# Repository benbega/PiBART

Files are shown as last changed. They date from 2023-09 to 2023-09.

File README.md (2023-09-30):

## Introduction
As a lifelong resident of the Bay Area, I have seen countless BART trains fly by, always giving off their signature high pitched howl as they barrel down the tracks. BART is a very unique urban transportation system, and although it is not the most efficient, I have grown to love riding it between the East Bay and San Francisco. 

The project outlined below is a fully custom model train, based off of the BART system. It was built to showcase skills in multiple facets of electrical engineering, as well as to be a homage to the legendary train.

A brief example of the train running can be seen [here](https://youtu.be/NTuRKBK8t7I)

## System Breakdown
At a high level, this project can be broken down into the following four major subsystems:

 1. Train Electronics
 2. Train Chassis
 3. Track Electronics
 4. Track Design

At the current time of writing, I am working on version 2 of the project, so the subsystem descriptions below will correspond to that version.

### Train Electronics
The train houses the entirety of the electronics it needs to operate autonomously. The main processing is all done on a Raspberry Pi 4B+, that is powered by a Geekworm X728 uninterruptable power supply (UPS) with two 18650 batteries. In order to know where it is located on the tracks, the Raspberry Pi is connected to an RC522 RFID sensor via SPI. The RFID tags are embedded in the tracks, and are manually preset to have "full speed", "slow", or "medium speed" values. After detecting these tags, the RFID sensor communicated back to the Raspberry Pi and the train enters the speed level corresponding to the tag.

In order to control the motor, the Raspberry Pi outputs logic signals to a custom PCB based around the L293D IC. The PCB has six logic inputs, external power input, two motor output terminals, and two status LEDs for debugging. The PCB is fully custom designed in KiCAD and was fabricated by PCBWay. The PCB can officially support up to 1A for each motor channel, but this number could possibly be higher in the future after some testing and possible integrating a cooling solution.

The train operates using a live third rail, which is currently running at 12V DC. Power from the third rail feeds in from two wires mounted on a side bracket (details on the mount can be found in the following section) and into the power delivery PCB and the Raspberry Pi UPS. The power is stepped down from the 12V to 5V with a simple DC-DC converter to match the needed input on the UPS. In the built configuration, the third rail is continually charging the battery cells on the UPS, which in turn power the Raspberry Pi. Since there are no metal tracks to ground the system, there is a hidden "fourth rail" running in the middle of the trackbed. An identical connection is made from the train to this rail in order to ground the system. 

The drivetrain of the train is based around a single DC motor that can be run in the 5-12V range. More about the drivetrain can be found in the *Train Chassis* section below.

### Train Chassis
The train chassis is entirely custom designed, using a mix of OnShape and TinkerCAD depending on the complexity of the parts. All elements of the chassis are 3d printed except for the ball bearings, which were purchased preassembled. The main chassis of the train is a flat plane with cutouts for the gears (more on those later). The top of the chassis features a slide mount for the Raspberry Pi and a vertical mounting bracket for the power delivery PCB, as well as a mount for the DC motor. In order to transfer power from the live third rail, there is a side mounted bracket to guide wires down from the Raspberry Pi and power delivery PCB. An identical mount runs through the gear cutout on the chassis to provide the ground line connections. The bottom of the chassis is reinforced with 3 extra strips of PLA running along the length of the train, while also featuring mounts for the bearings. The two axles are 1/4" diameter and have wheels friction fit on either end. The train wheels are conical in shape, with an exaggerated flange for extra stability on the small scale.

The drivetrain of the system consists of a DC motor with a 10 tooth gear and a 15 tooth gear mounted on the rear axle. A pulley is used to transfer power between the gears. The current gear ratio is still being iterated on, to find the right performance level for the scale.

### Track Electronics
The trackbed electronics are very simple in theory, but are currently difficult to maintain. The live third rail and grounding fourth rail are both 3d printed from PLA, with a layer of conductive copper tape stuck to the top of each. This copper tape preforms good enough for my needs, with about 5 ohms of resistance measured over 20 inches of rail. The downside of using the copper tape to add conductivity to the rails is its general structural weakness. The tape tears very easily, and wears out over time with the wires from the train car rubbing against it. Adding more tape on top of the worn tape can fix these problems, but also sometimes results in a loss of conductivity along the rail.

In order for the train to control itself, RFID tags are laid within the trackbed, between sleeper planks. Standard 13.56MHz RFID tags are used, in order to keep the system lower cost and less complex.

Power is provided to the third rail and grounding rail at one end of the trackbed, with a standard bench power supply.

### Track Design
The trackbed is a simple 3 rail design, with a small fourth rail running down the center of the tracks. The main rails are spaced with 3.375" between the center of each rail, with the third rail being 1.125" to the right of the trackbed. Each rail segment is 5" in length, and is supported by a sleeper plank at each end. The overall track dimensions were built out after the train chassis was assembled, to ease the design constraints on that part of the project.

## Current Features
The train currently can operate autonomously on a straight section of track, with the third rail running at 12V. A command is issued to the train to start moving initially, and then the Raspberry Pi takes over and controls the train's speed by reading RFID tags, as mentioned above. The train can slow down, speed up, and come to a complete stop autonomously. 

## Future Work
As of September 2023, I am working on optimizing the drivetrain of the system so it runs smoother along the rails. I am currently experimenting with ways of adding grip to the tracks, as well as with ways to better contact the third rail for more consistent power delivery. After these two parts of the system are finished, I will begin experimenting with the train's turn radius to find a suitable dimension to build curved sections of track. I anticipate this will be a longer process, and plan on building out a longer section of straight track simultaneously, to optimize the train control system and find the speed limits of the system. 

### End Notes
I will also be updating this GitHub repo with 3d models, code, images, and more over the coming weeks, so check back periodically if you are interested in the project. 

**I am also looking for work in the electrical engineering field, feel free to reach out if you have any leads.**

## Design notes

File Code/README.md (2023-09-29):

## Code Information

### GPIOZero
All code for this project is written in Python3, on a Raspberry Pi 4B+ running Raspbian. The [GPIOZero](https://gpiozero.readthedocs.io/en/stable/installing.html) library is used to simplify the scripting.

Instructions for installing and setting up GPIO Zero can be found [HERE](https://gpiozero.readthedocs.io/en/stable/installing.html).

### MFRC522
The [mfrc522](https://github.com/pimylifeup/MFRC522-python) library is used to connect with the RFID sensor, and can be downloaded with the following command in Raspbian:

    sudo pip3 install mfrc522

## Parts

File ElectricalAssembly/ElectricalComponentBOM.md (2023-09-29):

## Electrical Component BOM

This BOM does not include the parts to assemble the power delivery PCB. Please refer to the PCB schematics for that component list.

### Components:
1. Raspberry Pi 4B+ (4GB Model)
2. Geekworm Raspberry Pi X728 18650 UPS & Power Management Board
3. 2x Panasonic NCR18650GA 3450mAh 10A Battery
4. Generic 6-12V DC Motor
5. RC522 RFID Sensor
6. Generic 13.56MHz RFID tags
7. DC barrel jack adapter with screw terminals

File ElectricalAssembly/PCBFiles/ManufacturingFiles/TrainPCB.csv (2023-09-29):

Source: | D:\KiCadProjects\RaspiCar_PCB2\RaspiCar_PCB1.kicad_sch
Date: | 10/15/2022 9:34:41 PM
Tool: | Eeschema (6.0.4)
Generator: | C:\Program Files\KiCad\6.0\bin\scripting\plugins/bom_csv_grouped_by_value_with_fp.py
Component Count: | 17
Ref | Qnty | Value | Cmp name | Footprint | Description | Vendor
C1, C2, | 2 | 1uF | C | Capacitor_SMD:C_Elec_5x5.4 | Unpolarized capacitor
H1, H2, H3, H4, | 4 | MountingHole | MountingHole | MountingHole:MountingHole_2.2mm_M2 | Mounting Hole without connection
L293D1, | 1 | L293D | L293D | Package_DIP:DIP-16_W7.62mm | Quadruple Half-H Drivers
LED1, | 1 | LED1 | LED | LED_THT:LED_D5.0mm | Light emitting diode
LED2, | 1 | LED2 | LED | LED_THT:LED_D5.0mm | Light emitting diode
Motor_1, | 1 | MotorTerminal1 | Screw_Terminal_01x02 | TerminalBlock:TerminalBlock_Altech_AK300-2_P5.00mm | Generic screw terminal, single row, 01x02, script generated (kicad-library-utils/schlib/autogen/connector/)
Motor_2, | 1 | MotorTerminal2 | Screw_Terminal_01x02 | TerminalBlock:TerminalBlock_Altech_AK300-2_P5.00mm | Generic screw terminal, single row, 01x02, script generated (kicad-library-utils/schlib/autogen/connector/)
PWR_GND1, | 1 | PWR_GND | Conn_01x02_Male | Connector_PinHeader_2.54mm:PinHeader_1x02_P2.54mm_Vertical | Generic connector, single row, 01x02, script generated (kicad-library-utils/schlib/autogen/connector/)
R1, R2, | 2 | 3.3k | R | Resistor_THT:R_Axial_DIN0207_L6.3mm_D2.5mm_P7.62mm_Horizontal | Resistor
Raspi_Logic1, | 1 | PiLogicHeaders | Conn_01x06_Male | Connector_PinHeader_2.54mm:PinHeader_1x06_P2.54mm_Vertical | Generic connector, single row, 01x06, script generated (kicad-library-utils/schlib/autogen/connector/)
Raspi_PWR1, | 1 | RaspiPWR/GND | Conn_01x02_Male | Connector_PinHeader_2.54mm:PinHeader_1x02_P2.54mm_Vertical | Generic connector, single row, 01x02, script generated (kicad-library-utils/schlib/autogen/connector/)
ServoPWR1, | 1 | ServoPWR/GND | Conn_01x02_Male | Connector_PinHeader_2.54mm:PinHeader_1x02_P2.54mm_Vertical | Generic connector, single row, 01x02, script generated (kicad-library-utils/schlib/autogen/connector/)

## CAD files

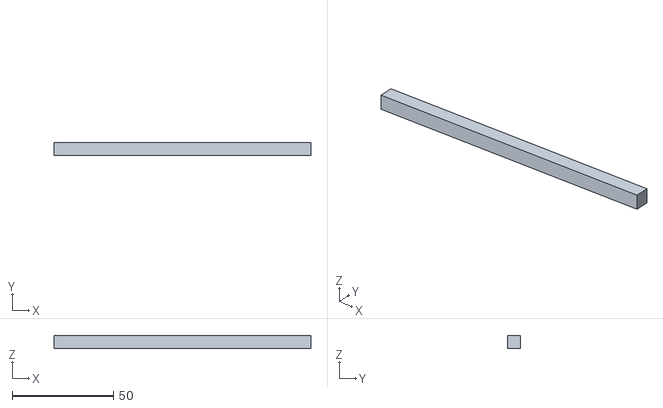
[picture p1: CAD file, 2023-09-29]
PhysicalAssembly/TrackAssemblyComponents/MainRail.stl
127.0 x 6.35 x 6.35

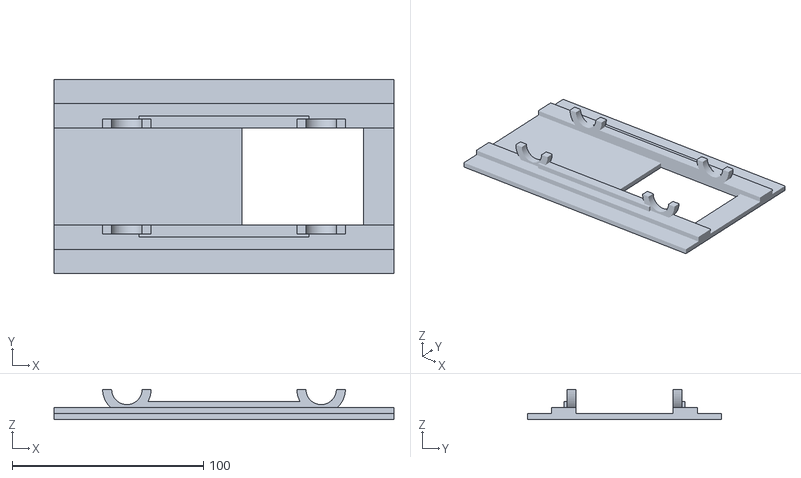
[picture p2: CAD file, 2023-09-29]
PhysicalAssembly/TrainAssemblyComponents/MainChassis.stl
177.8 x 101.6 x 15.9

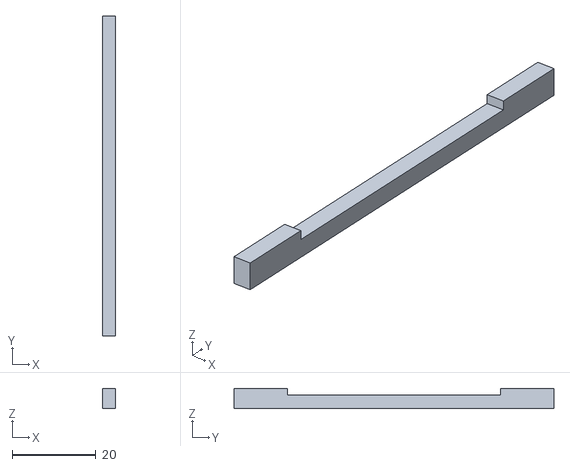
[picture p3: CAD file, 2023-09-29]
PhysicalAssembly/TrainAssemblyComponents/RFIDSensorMount.stl
3.18 x 76.2 x 4.76

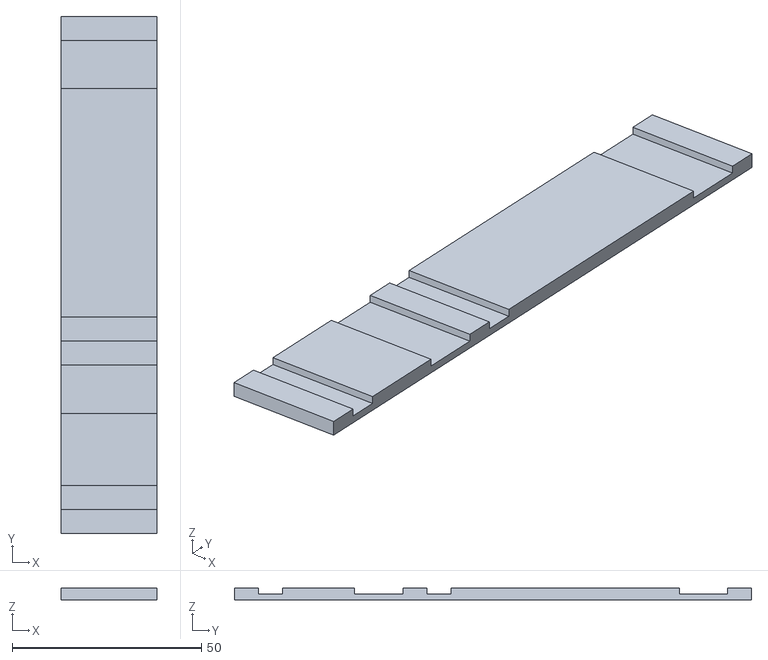
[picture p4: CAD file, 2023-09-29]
PhysicalAssembly/TrackAssemblyComponents/SleeperPlank.stl
25.4 x 136.5 x 3.17

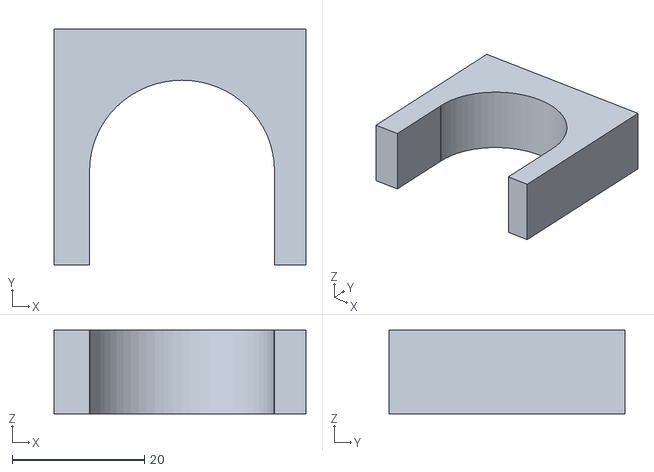
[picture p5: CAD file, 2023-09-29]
PhysicalAssembly/TrainAssemblyComponents/MotorMount.stl
38.1 x 35.7 x 12.7

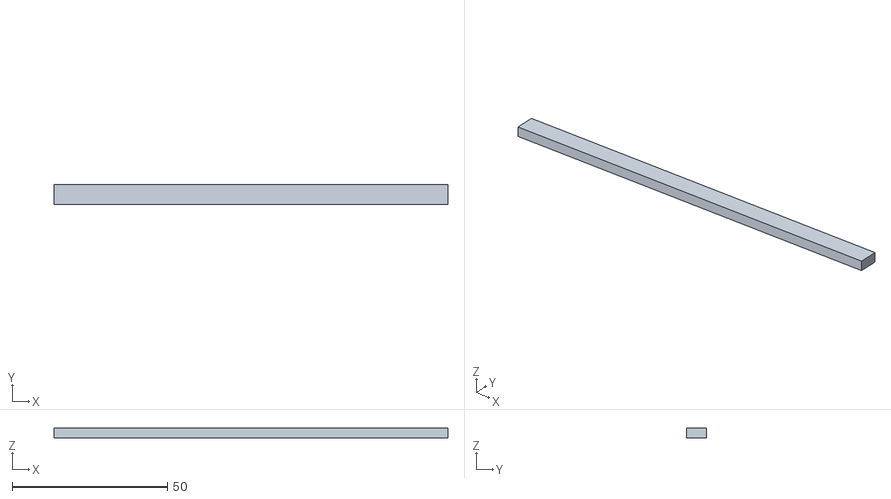
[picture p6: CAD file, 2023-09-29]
PhysicalAssembly/TrackAssemblyComponents/GroundingRail.stl
127.0 x 6.35 x 3.17

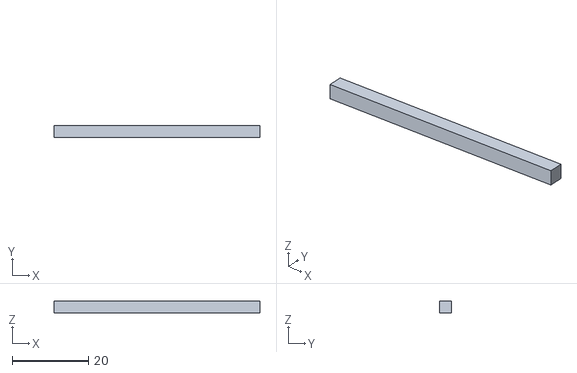
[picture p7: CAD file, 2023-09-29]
PhysicalAssembly/TrainAssemblyComponents/RaspberryPiMount.stl
54.0 x 3.18 x 3.17

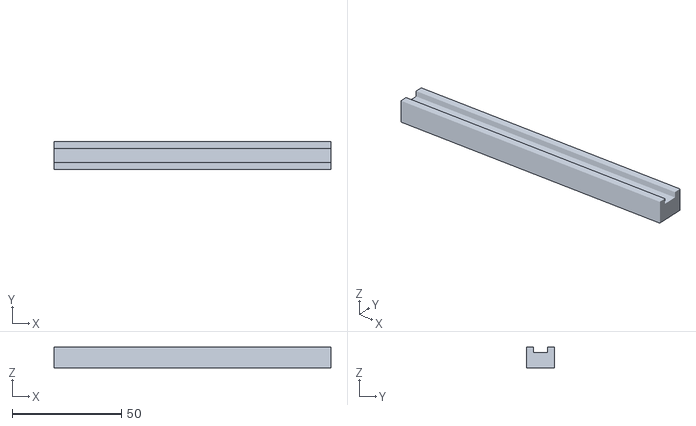
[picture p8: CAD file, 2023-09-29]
PhysicalAssembly/TrackAssemblyComponents/RailMount.stl
127.0 x 12.7 x 9.52

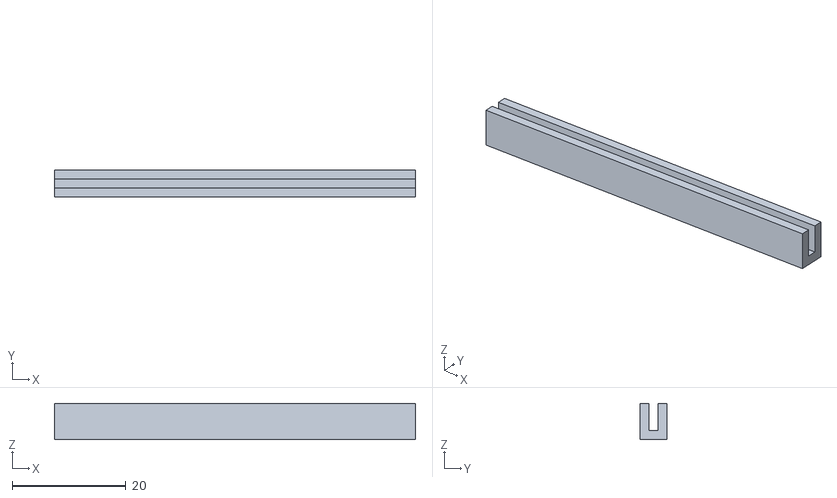
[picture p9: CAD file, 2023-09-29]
PhysicalAssembly/TrainAssemblyComponents/PowerDeliveryBoardMount.stl
63.5 x 4.76 x 6.35

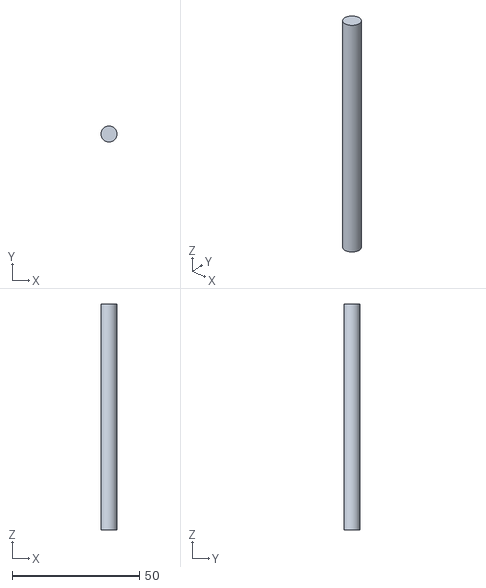
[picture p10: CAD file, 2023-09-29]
PhysicalAssembly/TrainAssemblyComponents/Axle.stl
6.35 x 6.35 x 88.9

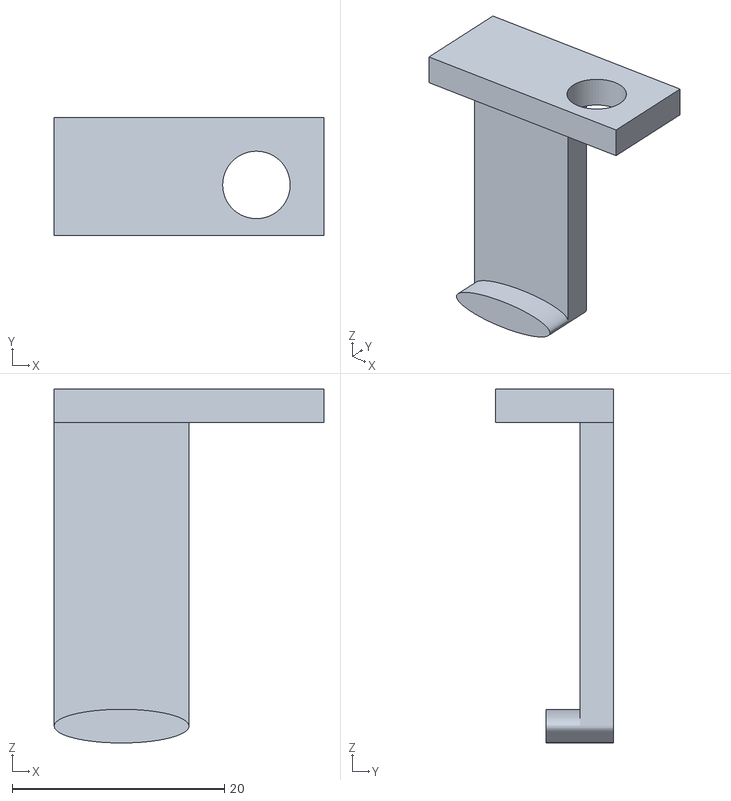
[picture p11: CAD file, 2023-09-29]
PhysicalAssembly/TrainAssemblyComponents/GroundingRailBoot.stl
25.4 x 11.1 x 33.3

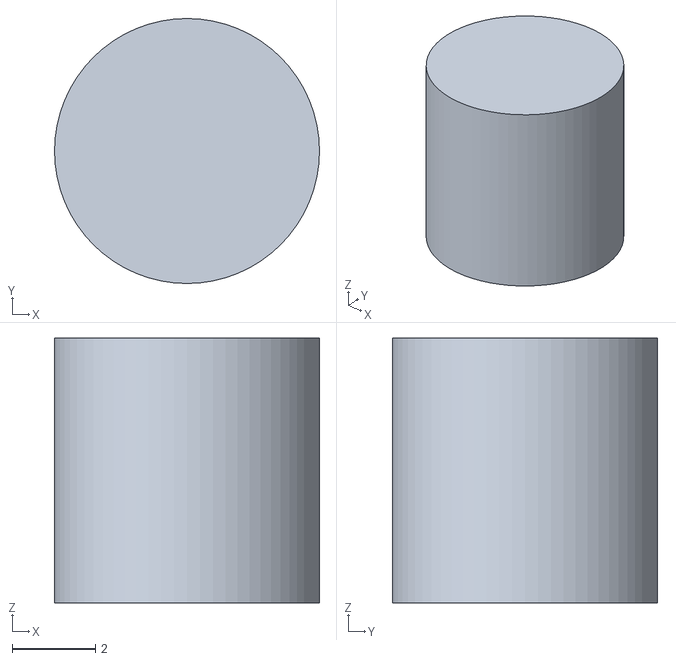
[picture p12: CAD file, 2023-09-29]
PhysicalAssembly/TrainAssemblyComponents/RailBootPivotMount.stl
6.35 x 6.35 x 6.35

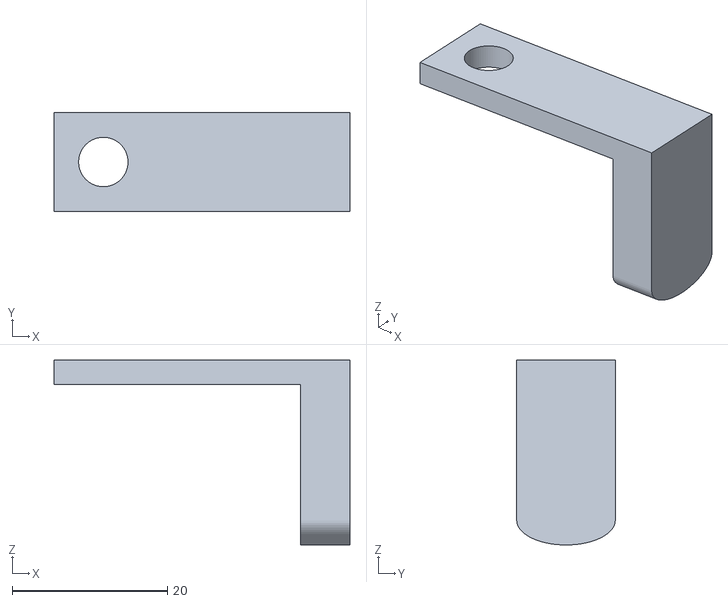
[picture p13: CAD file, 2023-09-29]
PhysicalAssembly/TrainAssemblyComponents/ThirdRailBoot.stl
38.1 x 12.7 x 23.8

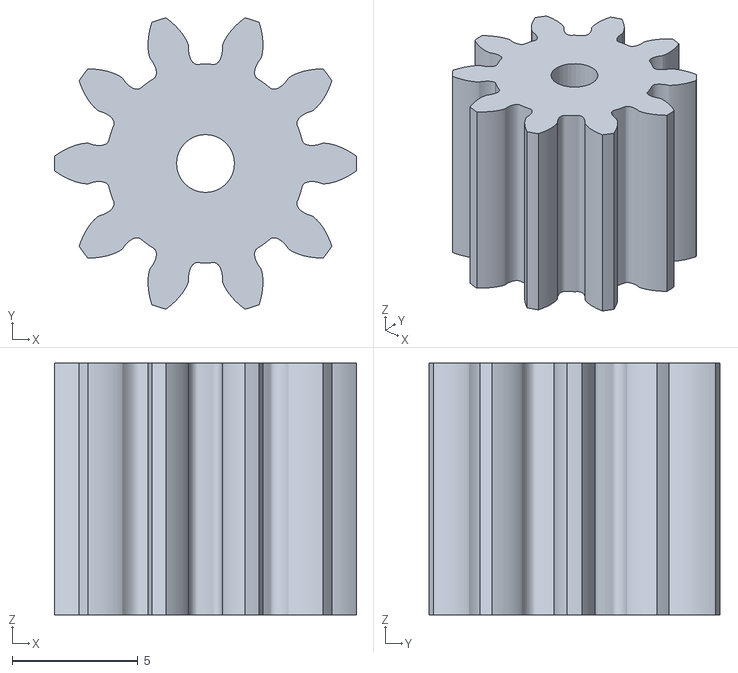
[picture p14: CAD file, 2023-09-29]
PhysicalAssembly/TrainAssemblyComponents/MotorGear_V2.stl
12.0 x 11.6 x 10.0

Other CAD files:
PhysicalAssembly/TrainAssemblyComponents/AxleGear.stl
PhysicalAssembly/TrainAssemblyComponents/MotorGear_V1.stl

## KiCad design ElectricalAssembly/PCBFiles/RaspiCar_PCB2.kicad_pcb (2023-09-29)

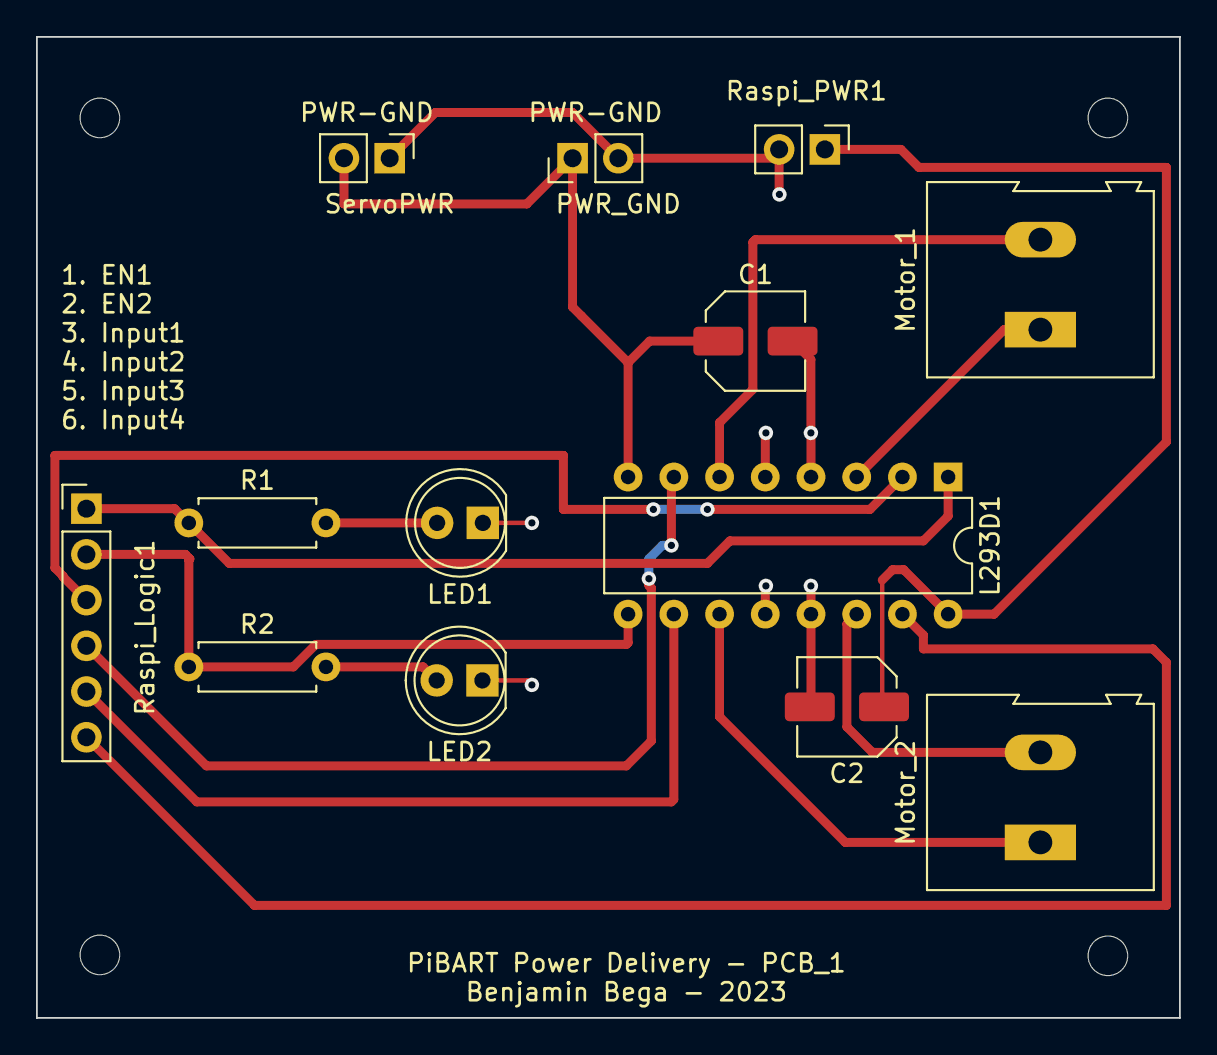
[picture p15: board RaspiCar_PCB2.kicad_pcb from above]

Board: 2 copper layers, 63.5 x 54.5 mm, 17 parts (0 on the bottom side), 15 nets.

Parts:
C1, C2: 1uF; C_Elec_5x5.4
H1, H2, H3, H4: MountingHole; MountingHole_2.2mm_M2
L293D1: L293D; DIP-16_W7.62mm
LED1: LED1; LED_D5.0mm
LED2: LED2; LED_D5.0mm
Motor_1: MotorTerminal1; TerminalBlock_Altech_AK300-2_P5.00mm
Motor_2: MotorTerminal2; TerminalBlock_Altech_AK300-2_P5.00mm
PWR_GND: PWR_GND; PinHeader_1x02_P2.54mm_Vertical
R1, R2: 3.3k; R_Axial_DIN0207_L6.3mm_D2.5mm_P7.62mm_Horizontal
Raspi_Logic1: PiLogicHeaders; PinHeader_1x06_P2.54mm_Vertical
Raspi_PWR1: RaspiPWR/GND; PinHeader_1x02_P2.54mm_Vertical
ServoPWR: ServoPWR/GND; PinHeader_1x02_P2.54mm_Vertical

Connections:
+5V: C2.1, L293D1.16 (VCC1), Raspi_PWR1.1
+7.5V: C1.1, L293D1.8 (VCC2), PWR_GND.1, ServoPWR.2
GND: C1.2, C2.2, L293D1.4 (GND), L293D1.5 (GND), L293D1.12 (GND), L293D1.13 (GND), LED1.1 (K), LED2.1 (K), PWR_GND.2, Raspi_PWR1.2, ServoPWR.1
unnamed: L293D1.1 (EN1,2), R1.1, Raspi_Logic1.1
unnamed: L293D1.2 (1A), Raspi_Logic1.3
unnamed: L293D1.3 (1Y), Motor_1.1
unnamed: L293D1.6 (2Y), Motor_1.2
unnamed: L293D1.7 (2A), Raspi_Logic1.4
unnamed: L293D1.9 (EN3,4), R2.1, Raspi_Logic1.2
unnamed: L293D1.10 (3A), Raspi_Logic1.5
unnamed: L293D1.11 (3Y), Motor_2.1
unnamed: L293D1.14 (4Y), Motor_2.2
unnamed: L293D1.15 (4A), Raspi_Logic1.6
unnamed: LED1.2 (A), R1.2
unnamed: LED2.2 (A), R2.2

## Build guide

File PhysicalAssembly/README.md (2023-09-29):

## Printing The Train Assembly

The .STL files in this folder make up the full physical assembly of the train. The only structural part that needs to be purchased are the ball bearings that the axles are fed through. All parts are affixed using standard super glue.

All components were printed in PLA, with a layer height of .24mm and a wall count of 3, with a gyroid infill structure at 10% total infill. These values can likely be changed according to your needs, as no parts undergo serious structural stress.

The current version of the train uses V2 of the motor gear, and requires a belt to transfer power from the motor to the axle. If you want to run the system without a belt, you can use v1 of the motor gear, but this may require a motor with more torque.

## Printing the track assembly

All track components can be snapped together and friction fit if printed without any warping. All settings can remain the same as the train assembly. The main rails come in two pieces in order to add more strength to the overall structure. To add more strength, the main rail pieces can be offset to go between two rail holders, letting you move the track around without taking it apart, if needed.

All structures have only been tested with the components listed in the parts list file. Modifications to the 3D models may have to be made if you want to switch components.

## Purchased Components

1. Rubber Sealed Bearings with 1/4" inner diameter and 5/8" outer diameter. Bearing width is 9/32".

This list will be amended if any other structural components are purchased for the train.
